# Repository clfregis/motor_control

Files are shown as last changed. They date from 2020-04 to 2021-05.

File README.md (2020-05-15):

# Motor Control Project
##### Prototype that controls a motor, get environment information and send it to an online database (firebase).

This project is a turnkey automation of a hopper in a industry. It consists of [hardware](hardware/) development of the board, development of the [firmware](firmware/) that manages the system, and a [web](web/) app that supervise and control the operation.
Basically, the board is able to control the motor, gather temperature and humidity information and send/receive data to/from a firebase database. How the system works is better explained in [firmware](firmware/) section.
______________
## 1. How to get things running

###  1.1. Hardware

First it is necessary to fabricate and mount the board:

1. Send GERBER files provided in [hardware](hardware/GERBER/) section to a PCB factory;
2. Buy components listed in [BOM](hardware/BOM.pdf) files;
3. Solder components in the board;

P.S.: It will be also necessary to buy a 5V power adapter (micro USB) to provide power to the board.

### 1.2. Web

Concurrently with hardware fabrication we can create a firebase project. We chose firebase because of its scalability and the built-in functions such as authentication and hosting.
There are some limitations in free plan, as shown [here](https://firebase.google.com/pricing?authuser=0). For MVP purposes, we will not be even closer to those limitations, but we can upgrade our plan if necessary.  
To create a project we need to have a google account, if you use Gmail, you already have one. Then access this [page](https://console.firebase.google.com/?pli=1), log in and create a `Realtime Database` (ust follows the steps in the tutorials, Google documentation is pretty awesome).
Then, add Firebase to your web app following these [instructions](https://firebase.google.com/docs/web/setup). **Attention!** In step 3, the HTMLs already have the SDKs. However, it is necessary to copy the snippet of our app's Firebase config object in the first line of `/web/js/main.js`.
After deploying the web app, we are ready!

### 1.3. Firmware

After mounting the hardware and deploying the web app, we are ready to build and flash the program in the ESP32. 

#### 1.3.1. Build
1. [Install the Espressif IoT Development Framework](https://github.com/espressif/esp-idf) or [link](https://docs.espressif.com/projects/esp-idf/en/latest/esp32/get-started/)
2. Make sure that the USB to UART driver of the development board is installed. In our case, the board uses [CP2102](https://www.silabs.com/products/development-tools/software/usb-to-uart-bridge-vcp-drivers)
3. Clone this repo: `git clone ...`
4. Inside the firmware folder, configure: `make menuconfig`
5. Build: `make all`
6. Flash: `make flash`

* Build & flash & monitor: `make flash monitor`

P.S.: If you get an error like: **"make" is not recognized as a internal or external command**. Try to use `idf.py` instead of `make` command.

Note: In step 3 you need to change some config values, for example:

* `Serial flasher config`. 
	+ `Default serial port`: Type the port at which the ESP32 is connected (e.g. COM3). If this option does not appear, just ignore it, the port will be automatically detected. 
	+ `Default baud rate`: Select 921600 for a faster flashing time.
* `Motor Configuration`. 
	+ `Motor Value`: Type the firebase child at which this ESP32 will send its data (e.g. motor_2).
	+ `Firebase address`: Type the firabase address without 'http://' (e.g. name_project.firebaseio.com). 
	+ (Optional) Change the `SP Time in seconds` value (It can be changed later via web app).
	+ `Timezone`: Select the time zone accordingly to your region.
	+ (Optional) `Log prints for Debug`, check it only if you want to see debug logs using the command prompt.
* `Example Connection Configuration`
	+ `Connect using`: Select WiFi.
	+ `WiFi SSID`: Type the SSID of your WiFi station.
	+ `WiFi Password`: Type the password of your WiFi station.

Save the changes and proceed to step 4.

### 1.4. Future Implementations

+ Update the daily and continuous operating times upon booting. Useful if the systems crashes during the day, because when it restarts it resets these values.
+ Every night at midnight, send the daily operating times to the server. Create a page on web app to display these values in bar graph format.
+ Implement a supervisor to reset the system if have problems with WiFi connection.

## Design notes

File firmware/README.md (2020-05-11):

# Firmware

______________

Well, depending on the project, the firmware development can be the most time consuming and complex task to do.
For this project, we used free RTOS mostly because it was necessary to deliver a robust application. Dealing with real motors, safety is a big concern.
For the microcontroller, we used ESP32, a very very powerful device (Arduinos are ancient technology compared to it). I will not get into too much detail regarding the specifications of the device. In general it has WiFi and Bluetooth connections, it is dual core, have some flash memory (used to store the SSID and Password of WiFi Networks) and can be easily programmed to work in Low Power.
Our application consists of a motor control of a hopper, based on the state of a NC switch. Basically, when the switch is not pressed (digital Low) the motor is running and when the switch is pressed (digital High) the motor stops. The system is also capable of retrieve the temperature and humidity of the environment using a DHT22 sensor. On top of that, we count the operation time of the motor. The operation time, temperature and humidity are stored internally and every minute it is sent to a database (we used firebase from Google).
We use the information of operation time for two things:

1. Stop the motor if it stays running for a long period of time (named SP time). Basically, when the motor runs for a long period of time, it means that the line breaks and material is being spilled outside the hopper.
2. Record the daily operation of the motor to cross check the material used daily.

## Global Variables

The global variables as in an ordinary code can be manipulated by all functions and all tasks. It is not good practice to use global variables in free RTOS, unless you really know what you are doing. The risk of a task change the value of a variable in the middle of execution of other task that also manipulates this same variable is high. We can use semaphores, queues and other things to maintain our code safe, however, in our case, there is only one task that ever writes to the variable (although many can read from it), then a global variable should not cause a problem.  
The variables, its type and its purpose are organized in the table below:

| Variable name | Type | For what it is used |
|---|---|---|
| temperature | uint8_t | Store the reading of the temperature |
| humidity | uint8_t | Store the reading of the humidity | 
| motorStatus | uint8_t | Store the status of the motor. 1-Running, 2-Halted, 0-Stopped |
| runningTime | time_t | Store the operation time of the motor since midnight |
| continuousRunningTime | time_t | Store the continuous operating time of the motor since the last time it was off |
| now | time_t | Store the current time of the system every time it is called by time() function |
| timeInfo | struct tm | Actually it is a struct not a variable, it stores the time in a very detailed way by localtime() function, taking into consideration timezone |
| url[65] | char | Store the firebase url to do the HTTP requests |
| bufferData[60][120] | char | Store the Data that will be sent to the database, up to 60 different POST request |
| bufferCounter | uint8_t | Counter used to do a loop when sending data to database |
| strftime_db[26] | char | For debug only, store a string with time in a human readable format |
| *motorAddress | static const char | Stores the value of the motor to create the url on connection with thedatabase. It is defined when programming the board on `menuconfig`, thus we pass`CONFIG_motorValue` to it |
| *firebaseAddress | static const char | Stores the address of the firebase to create the url on connection with thedatabase. It is defined when programming on `menuconfig`, thus we pass`CONFIG_firebaseAddress` to it |
| spTimesec | uint32_t | Stores the SP time of the motor. It can be changed by front end or when programming, thus we pass `CONFIG_SPTimesec` to it when programmin the board. |
| frontEndReset | uint8_t | Used to reset the motor by front end |
| updateBufferCounter | uint8_t | Used to count a defined number of seconds until the next update of the buffer |
| updateDailyFlag | bool | Used to check if the daily updating was already executed |
| gpio_evt_queue | xQueueHandle | Used to create a queue to handle GPIO events |

## Tasks

In free RTOS, we have tasks, which we can think of as pieces of codes that can run concurrently. The definition of a task is much more complex and I recommend to read the Kolban's book on ESP32 where he explains in details the architecture of a task. One thing to keep in mind is that tasks have priorities (the higher the number, higher is its priority), thus, let's say we have two tasks: A (priority 2) and B (priority 3). If A is running and B is ready to run, the task A will stop and then the task B will run. When B finishes, the task A will resume from where it stopped.
All tasks are shown in the table below.

| Task name | Priority |Function | Writes to  | Reads from |
|---|---|---|---|---|
| motor_control_task | 4 | Controls the motor operation, based on the state of NC switch, motor status and reset button|motorStatus, continuousRunningTime and frontEndReset|motorStatus|
| clock_task | 3 | Correct the drift time daily around midnight and reset the operation times|runningTime, continuousRunningTime,now and timeInfo| |
| motor_supervisor_task | 2 | Every other second reads temperature and humidity, updates the operation times and update the buffer|runningTime, continuousRunningTime, motorStatus, frontEndReset, bufferData size and bufferCounter |motorStatus and frontEndReset |
| database_task | 1 | Every other minute sends the buffer data to database, read SP time modifications in front end, update front end status and update daily status|url|size, bufferData, spTime and frontEndReset|

## Functions

|Function Name|Discussion|Parameters|Result|
|---|---|---|---|
|bufferUpdate|Take the values of tempertature, humidity, now, runningTime, motorStatus and continuousRunningTime and fetch to buffer|void|bufferData with a new value|
|update_sntp_time|Connect to SNTP server and update system time|void|System time synchronized with UTC time|
|get_last_value|It takes the last operation times for the current day|void|continuousRunningTime and runningTime updated|
|update_frontEndStatus|Connect to a child on firebase accordingly to the motorAddress and retrieve its status|motorStatusAddress pointer to motorAddress|frontEndStatus with a new value|
|get_sp_time|Connect to a child on firebase accordingly to the motorAddress and retrieve the SP time if it changed since last reading|motorSPAddress pointer to motorAddress|spTimesec with a new value|
|time_sync_notification_cb|For Debug purposes. Log on screen when the time is synchronized|*tv struct ??|Log on screen|
|obtain_time|Update now and timeInfo variables with current system time|local_now and local_timeinfo pointers to now and timeInfo variables|now and timeInfo with updated values|
|wifi_connection_start|Configures the WiFi variables|void|Returns error if configuration fails|
|wifi_connection_begin|Connect to WiFi in previous configured SSID|void|Returns error if connection fails|
|wifi_connection_end|Close the connection from WiFi network|void|Returns error if it fails|
|gpio_isr_handler|Runs every time an interrupt occurs, sending events to a queue|arg contains the number of gpio at wich the hardware interrupt happened|Send events to gpio event queue|
|http_event_handler|Handles HTTP event queue|evt pointer to HTTP event|Log accordingly to the content of event ID|
| update_daily | Sends data to database | motorDailyAddress Pointer to motorAddress| Database with updated daily operation information| 

## Future implementations

+ Separate files (one for function declarations and function definitions), one for tasks, etc.
+ Change temperature and humidity from uint_8 to float variables to have more precision.
+ Use some sort of automatic documentation generation from comments.

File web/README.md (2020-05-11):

# Web
______________

The `web` folder is basically the front end. It consists of the web interface, which request and send data to the firebase server.

## HTML

 The structure of HTML files is:
 
 	|-index.html
 	|---motor_1.html
 	|---motor_2.html
 	|---motor_3.html
 	|---motor_4.html
 	|-404.html (Generated by firebase)

 + `index.html` contains the intro page of the web app, which is a lateral bar and two cards. The first card contains links to open the motors pages. The second card will contain the input form to register new motors.
 + `404.html` contains the error page
 + `motor_X.html` are pages that show the graphs of each motor (temperature, humidity and operating) with respect to time. It is possible to zoom in the graphs using the mouse cursor or by choosing an especific date on the datepicker form. There are also cards that contain (almost) realtime information of the motor, such as its current state, temperature, daily operating times, etc. In this cards, it is possible to reset halted motors and change the SP time.

## CSS

 The structure of CSS files is:
 
 	|-all.css
 	|-dashboard.css
 	|-jquery-ui.css
 	|-reset.css

These files have all the styling definitions of every classes and objects inside the HTML files. The jquery-ui.css is special, it contains information specifically of the datepicker.

## JS

There are only one JS file, the `main.js`, which contains the interface to the firebase database and other stuff such as loading animations, functions to draw [zing charts](https://www.zingchart.com/download) and do [automatic zoom](https://www.zingchart.com/gallery/line-chart-with-zoom-buttons), functions to work with UNIX timestamp, etc. Please refer to [firebase documentation](https://firebase.google.com/docs/reference/js?authuser=0) to understand some of the functions used there. To use zing charts, please also check its [documentation](https://www.zingchart.com/docs/api/json-configuration)

## Firebase

For Firebase hosting, please refer to its [documentation](https://firebase.google.com/docs/hosting/?authuser=0#implementation_path). With respect to the database, we have pretty much the following structure:

	root {
		motor_1: {
			- M61_vCVgkNTwwjbF5MB : {
				CO: 60,
				D: 1588107627,
				DO: 60,
				H: 88,
				S: 1,
				T: 31
			},
			...
		},
		motor_2: {...},
		motor_3: {...},
		motor_4: {...},
		sp_time: {
			motor_1 : 200,
			motor_2 : 750,
			motor_3 : 800,
			motor_4 : 300
		},
		front_end_reset_status: {
			motor_1 : 200,
			motor_2 : 750,
			motor_3 : 800,
			motor_4 : 300
		},
		daily: {
			motor_1 : {
			- M61_vCVgkNTwwjbF5MB : {
				D: 1588107627,
				DO: 60
			},
		}

The `motor_X` childs receive informations from motors every minute. Back End writes to this child and Front End only reads. the format is the following:

	- M61_vCVgkNTwwjbF5MB : {
				CO: 60,
				D: 1588107627,
				DO: 60,
				H: 88,
				S: 1,
				T: 31
			},

 `- M61_vCVgkNTwwjbF5MB` is a timestamp key automatically created by firebase. It occurs because we are doing POST requests with this information. Each minute, up to 60 of this blocks are updated to the database by the motors, where:
	 
| Code 	| Meaning 	| Unit 	|
|---	|---	|---	|
| CO 	| Continuous Operation 	| Seconds 	|
| D 	| Date 	| UNIX timestamp format UTC timezone 	|
| DO 	| Daily Operation 	| Seconds 	|
| H 	| Humidity 	| % 	|
| S 	| Status 	| 0 - Off, 1 - Running, 2 - Halted 	|
| T 	| Temperature 	| ºC 	|

The `sp_time` child have the information of SP time operation of each motor. Front End writes to this child and Back End only reads (every minute).

The `front_end_reset_status` child is used by the Front End to reset the motor via the front end in case it is halted.

The `daily` child is used to store the information of the daily operation time of a day. Front end use this data to create a bar graph that is updated daily between 23:30 and 23:59 by the back end.

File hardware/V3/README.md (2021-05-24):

# Hardware V3
______________

## 3D Model of the board when mounted

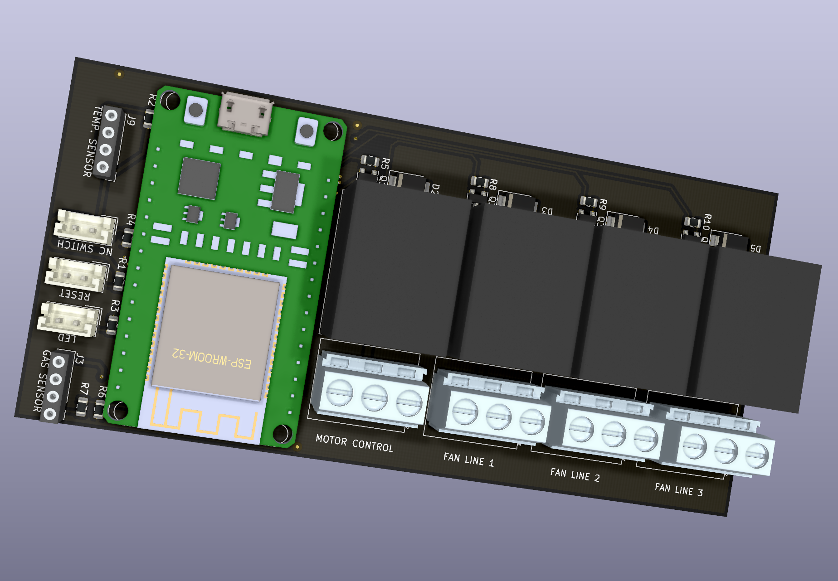
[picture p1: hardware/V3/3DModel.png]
3D Model


______________

The `hardware` folder has all necessary files to produce and mount the hardware part of the project as can be seen on the table below.

|File/Folder |Function |
|---|---|
|3DModel.png |3D Model picture of the mounted board. |
|ibom.html |Bill of Materials, all components necessary to build the project. |
|ESP32-pinout-mapping.png |Pinout of the development board used in the project. |
|gerber.zip |Output files to produce the PCB in the factory. The industries accept .zip files.|
|Schematic.pdf |File that shows how the components are connected to each other in the board. |
|Layout.pdf |Mechanical design |

We have two options when mounting this board, one is to solder the ESP32 Development Board directly to PCB, other is use female headers. The latter is better because it will be possible to remove the board easily if you want to.
It is important to be aware of what model of ESP 32 Development board to use. This project was designed to be compatible with [DoIT ESP32 DevKit V1](https://docs.platformio.org/en/latest/boards/espressif32/esp32doit-devkit-v1.html) with 30 pins (some development boards have more pins). The pinout is shown below:
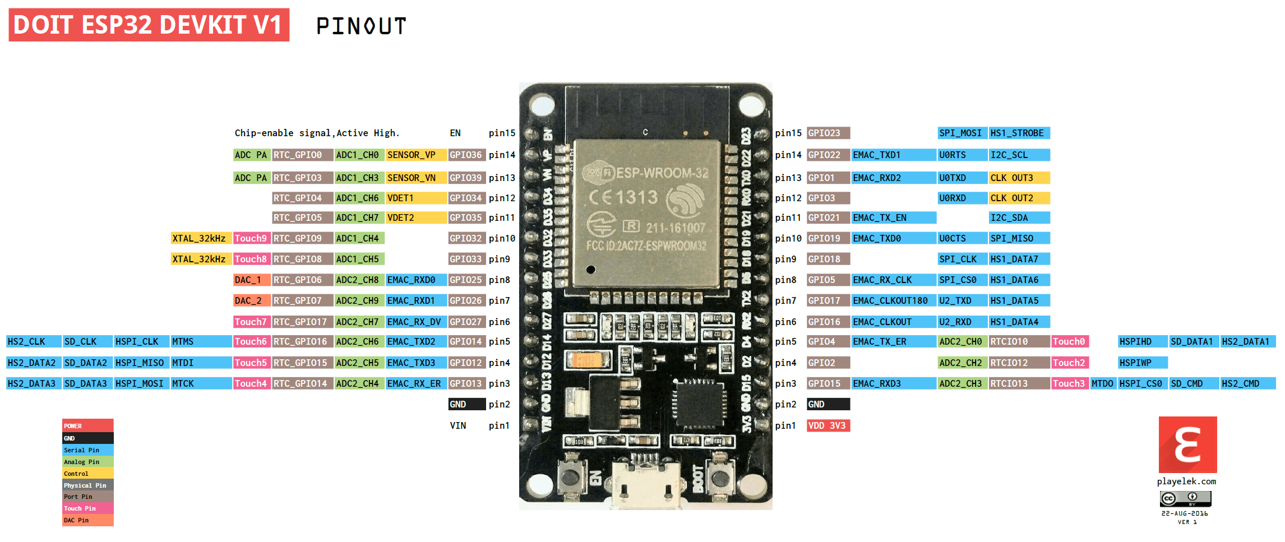
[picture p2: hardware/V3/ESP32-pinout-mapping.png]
DoIT ESP32 DevKit V1


## BOM

[Interactive BOM link](ibom.html)
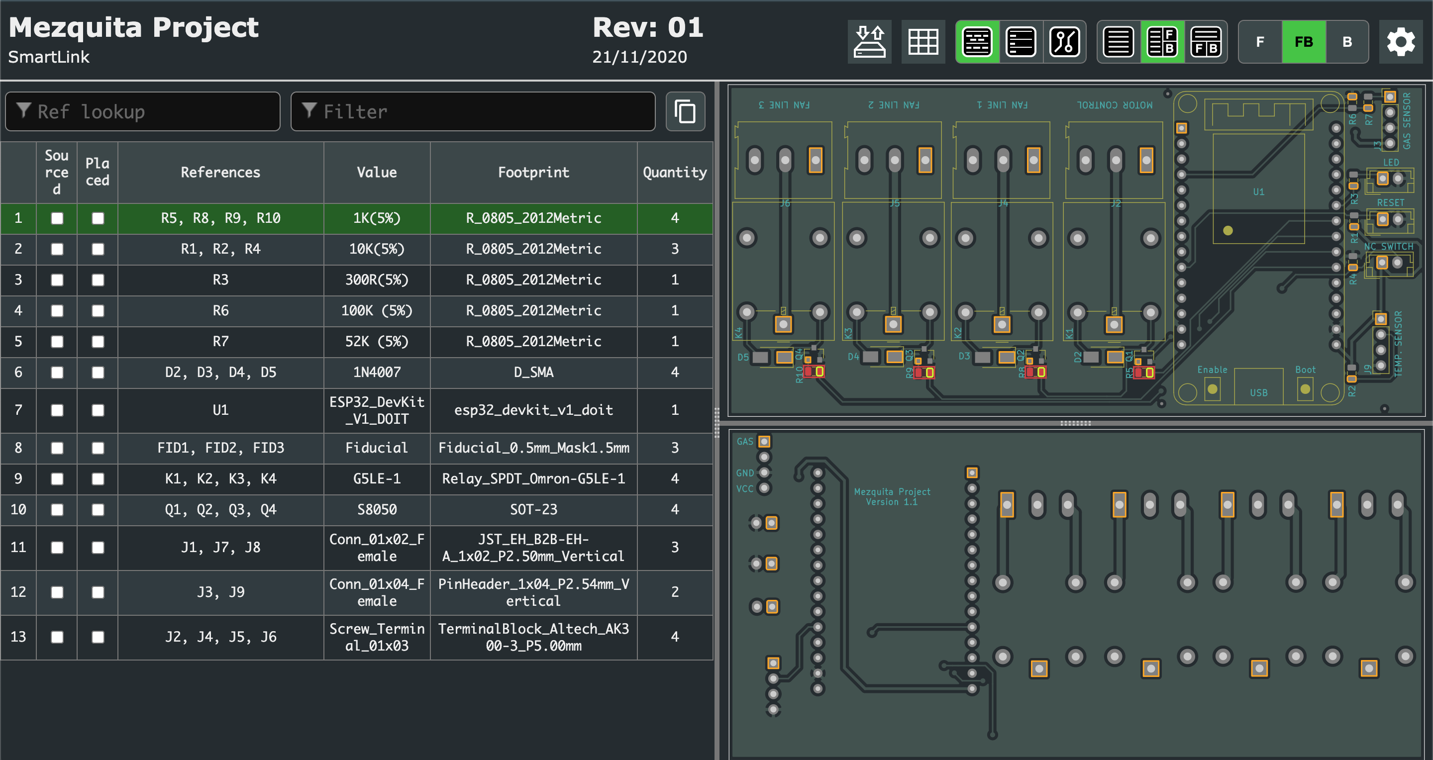
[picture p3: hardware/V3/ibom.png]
ibom


## Future Implementations

+ Add [licensing](https://forum.mysensors.org/topic/3096/open-hardware-licensing).
+ Add LEDs to show operation processes (blink fast when looking for internet connection, blink slow when is working properly, etc).
+ Instead of using DoIT ESP32 DevKit V1 board, put the ESP32 microcontroller directly into PCB.

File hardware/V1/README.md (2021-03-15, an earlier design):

# Hardware V1
______________

## 3D Model of the board when mounted

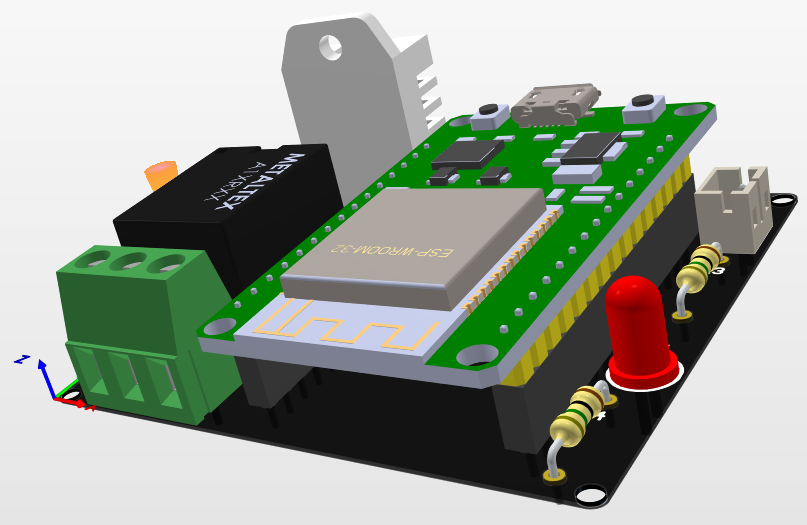
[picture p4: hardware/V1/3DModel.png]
3D Model


______________

The `hardware` folder has all necessary files to produce and mount the hardware part of the project as can be seen on the table below.

|File/Folder |Function |
|---|---|
|GERBER |Output files to produce the PCB in the factory. |
|3DModel.png |3D Model picture of the mounted board. |
|BOM.csv |Bill of Materials, all components necessary to build the project. |
|BOM.pdf |Bill of Materials, all components necessary to build the project. |
|Board 3D.pdf |3D Model picture of the mounted board. Open in Acrobat Reader. |
|Drill.Cam |Mechanical positioning and sizes of holes in the board in CAM format. |
|ESP32-pinout-mapping.png |Pinout of the development board used in the project. |
|GERBER.zip |Output files to produce the PCB in the factory. The industries accept .zip files.|
|General_Schematic.pdf |File that shows how the components are connected to each other in the board. |
|Layers.Cam |Mechanical positioning and sizes of all layers in the board in CAM format. |
|Mechanical Bot Mirrored.pdf|Mechanical designes with sizes and holes distances. |
|Mechanical Bot.pdf |Mechanical designes with sizes and holes distances. |
|Mechanical Top.pdf |Mechanical designes with sizes and holes distances. |	

For this specific project we do not have any special part, no SMD nor difficult components to find and use. We have two options when mounting this board, one is to solder the ESP32 Development Board directly to PCB, other is use female headers. The latter is better because it will be possible to remove the board easily if you want to.
It is important to be aware of what model of ESP 32 Development board to use. This project was designed to be compatible with [DoIT ESP32 DevKit V1](https://docs.platformio.org/en/latest/boards/espressif32/esp32doit-devkit-v1.html) with 30 pins (some development boards have more pins). The pinout is shown below:
DoIT ESP32 DevKit V1

## BOM

|Designator|Comment |Description |Quantity|Value |Reference Link |Datasheet|
|---|---|---|---|---|---|---|
|D1 |Diode |Rectifier Diode 1N4007 |1 |1N4007|[1N4007](https://lcsc.com/product-detail/Others_GW-1N4007_C331633.html) |[1N4007](Datasheet/1N4007.pdf)|
|L1 |Red LED |5mm Red LED |1 | |[5mm Red LED](https://lcsc.com/product-detail/Others_TOGIALED-TJ-L5FYTGHRMBCSFLC4R-A5_C331027.html)|[5mm Red LED](Datasheet/RED%20LED.pdf)|
|Q1 |Transistor |NPN General Purpose Amplifier |1 |PN2222|[PN2222](https://lcsc.com/product-detail/Transistors-NPN-PNP_ON-Semiconductor-ON-PN2222ATFR_C184875.html)|[PN2222](Datasheet/PN2222.pdf)|
|R1 |Resistor |1/4 W Resistor 1K 5% |1 |1K |[1K](https://lcsc.com/product-detail/Carbon-Film-Resistors_CCO-Chian-Chia-Elec-CF1-4W-1KR-5-T52_C120055.html)|[1K](Datasheet/1K%201_4W%20Resistor.pdf)|
|R2, R3, R5|Resistor |1/4 W Resistor 10K 5% |3 |10K |[10K](https://lcsc.com/product-detail/Carbon-Film-Resistors_UNI-ROYAL-Uniroyal-Elec-CFR0W4J0103A50_C61299.html)|[10K](Datasheet/10K%201_4W%20Resistor.pdf)|
|R4 |Resistor |1/4 W Resistor 300R 5% |1 |300R  |[300R](https://lcsc.com/product-detail/Carbon-Film-Resistors_UNI-ROYAL-Uniroyal-Elec-CFR0W4J0301A50_C69881.html)|[300R](Datasheet/300R%201_4W%20Resistor.pdf)|
|RLY1 |Relay |5V Relay |1 | |[5V](https://lcsc.com/product-detail/Relays_SRD-05VDC-SL-C_C35449.html)|[5V](Datasheet/5V%20Relay.pdf)|
|S1 |Switch |Switch Pushbutton |1 | |[Switch](https://lcsc.com/product-detail/Tactile-Switches_Korean-Hroparts-Elec-K2-6639DP-V4SW-04_C89914.html)|[Switch](Datasheet/Switch%20Pushbutton.pdf)|
|T1 |Terminal |3-Way Screw Terminal |1 | |[Screw Terminal](https://lcsc.com/product-detail/Screw-terminal_DIBO-DB126V-5-0-3P_C395850.html)|[Screw Terminal](Datasheet/ScrewTerminal.pdf)|
|T2 |JST |JST Male Board Connector |1 | |[JST Connector](https://lcsc.com/product-detail/Wire-To-Board-Wire-To-Wire-Connector_JST-Sales-America_B2B-XH-2-LF-SN_JST-Sales-America-B2B-XH-2-LF-SN_C158014.html)|[JST Connector](Datasheet/JST%20Connector.pdf)|
|T3,T4 |Not in Schematic (Optional)|Female Pin Header 15x2.54mm (Pitch)|2 | |[Pin Header](https://lcsc.com/product-detail/Pin-Header-Female-Header_Ckmtw-Shenzhen-Cankemeng-C124408_C124408.html)|[Pin Header](Datasheet/Female%20Pin%20Header.pdf)|
|U1 |ESP32 Dev Kit V1 |DoIT Development board |1 | |[ESP32](https://produto.mercadolivre.com.br/MLB-1027131279-esp32-placa-de-desenvolvimento-wifi-bluetooth-esp32s-_JM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)|[ESP32](https://github.com/SmartArduino/SZDOITWiKi/wiki/ESP8266---ESP32)|
|U2 |DHT22 |Temperature and Humidity Sensor |1 | |[DHT22](https://produto.mercadolivre.com.br/MLB-1144947807-sensor-de-temperatura-e-umidade-dht22-_JM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)|[DHT22](Datasheet/DHT22.pdf)|

## Future Implementations

+ Add [licensing](https://forum.mysensors.org/topic/3096/open-hardware-licensing).
+ Change PTH to SMD components to reduce size.
+ Add LEDs to show operation processes (blink fast when looking for internet connection, blink slow when is working properly, etc).
+ Instead of using DoIT ESP32 DevKit V1 board, put the ESP32 microcontroller directly into PCB.

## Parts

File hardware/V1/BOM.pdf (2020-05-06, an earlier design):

Designator | Comment | Description | Quantity | Value | Reference Link
D1 | Diode | Rectifier Diode 1N4007 | 1 | 1N4007 | 1N4007
L1 | Red LED | 5mm Red LED | 1 | | 5mm Red LED
Q1 | Transistor | NPN General Purpose Amplifier | 1 | PN2222 | PN2222
R1 | Resistor | 1/4 W Resistor 1K 5% | 1 | 1K | 1K
R2, R3, R5 | Resistor | 1/4 W Resistor 10K 5% | 3 | 10K | 10K
R4 | Resistor | 1/4 W Resistor 300R 5% | 1 | 300R | 300R
RLY1 | Relay | 5V Relay | 1 | | 5V
S1 | Switch | Switch Pushbutton | 1 | | Switch
T1 | Terminal | 3-Way Screw Terminal | 1 | | Screw Terminal
T2 | JST for the external switch | JST Male Board Connector | 1 | | JST Connector
T3,T4 | Not in Schematic (Optional) | Female Pin Header 15x2.54mm (Pitch) | 2 | | Pin Header
U1 | ESP32 Dev Kit V1 | DoIT Development board | 1 | | ESP32
U2 | DHT22 | Temperature and Humidity Sensor | 1 | | DHT22

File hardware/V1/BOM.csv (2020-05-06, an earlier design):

Designator | Comment | Description | Quantity | Value
D1 | Diode | Rectifier Diode 1N4007 | 1 | 1N4007
L1 | Red LED | 5mm Red LED | 1
Q1 | Transistor | NPN General Purpose Amplifier | 1 | PN2222
R1 | Resistor | 1/4 W Resistor 1K 5% | 1 | 1K
R2, R3, R5 | Resistor | 1/4 W Resistor 10K 5% | 3 | 10K
R4 | Resistor | 1/4 W Resistor 300R 5% | 1 | 300R
RLY1 | Relay | 5V Relay | 1
S1 | Switch | Switch Pushbutton | 1
T1 | Terminal | 3-Way Screw Terminal | 1
T2 | JST | JST Male Board Connector | 1
T3,T4 | Not in Schematic (Optional) | Female Pin Header 15x2.54mm (Pitch) | 2
U1 | ESP32 Dev Kit V1 | DoIT Development board | 1
U2 | DHT22 | Temperature and Humidity Sensor | 1

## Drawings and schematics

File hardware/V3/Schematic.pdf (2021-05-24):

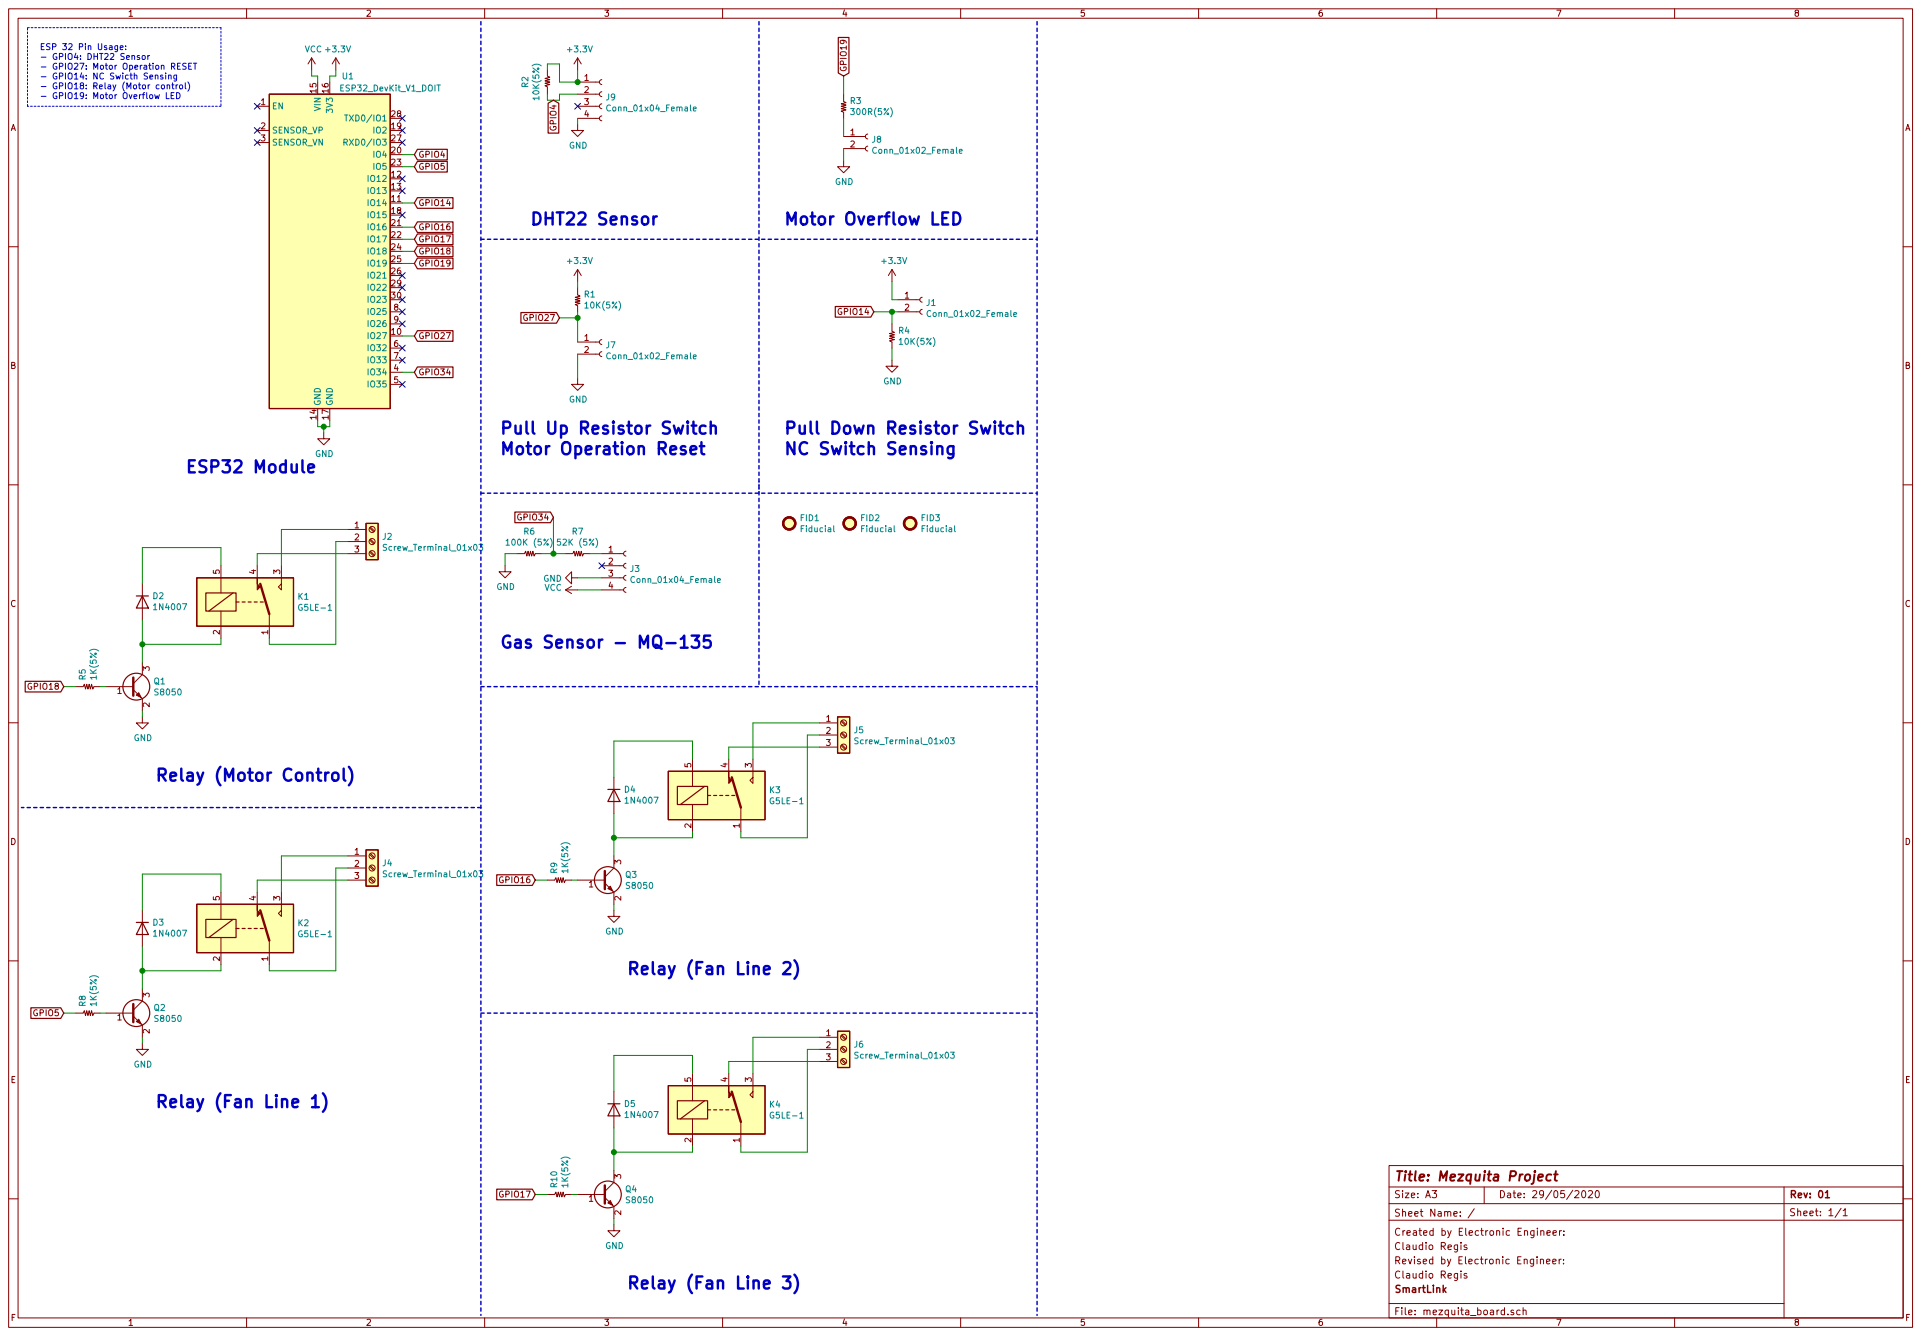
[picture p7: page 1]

ESP 32 Pin Usage: - GPIO4: DHT22 Sensor

Pull Up Resistor Switch
Motor Operation Reset

File: mezquita_board.sch Sheet Name: / SmartLink Claudio Regis

Claudio Regis
Revised by Electronic Engineer:

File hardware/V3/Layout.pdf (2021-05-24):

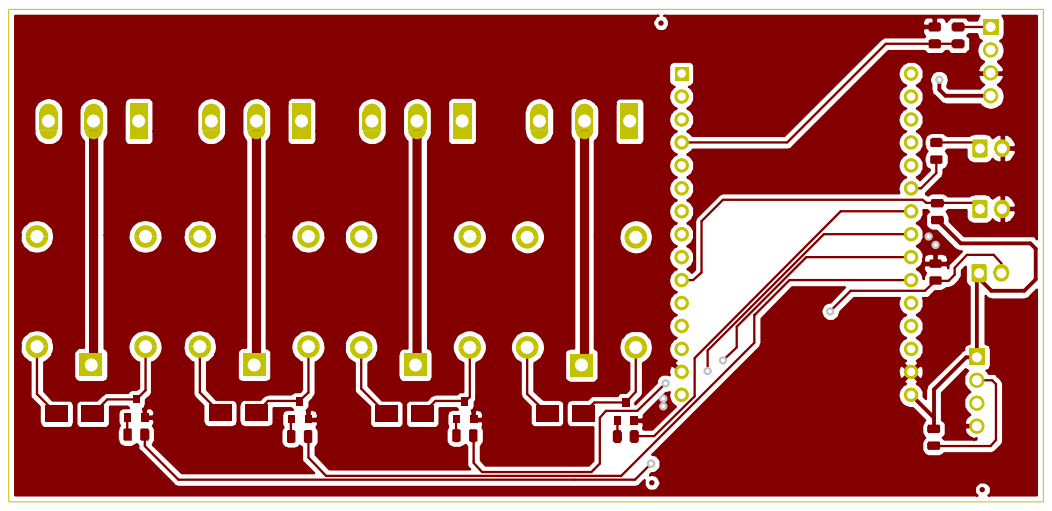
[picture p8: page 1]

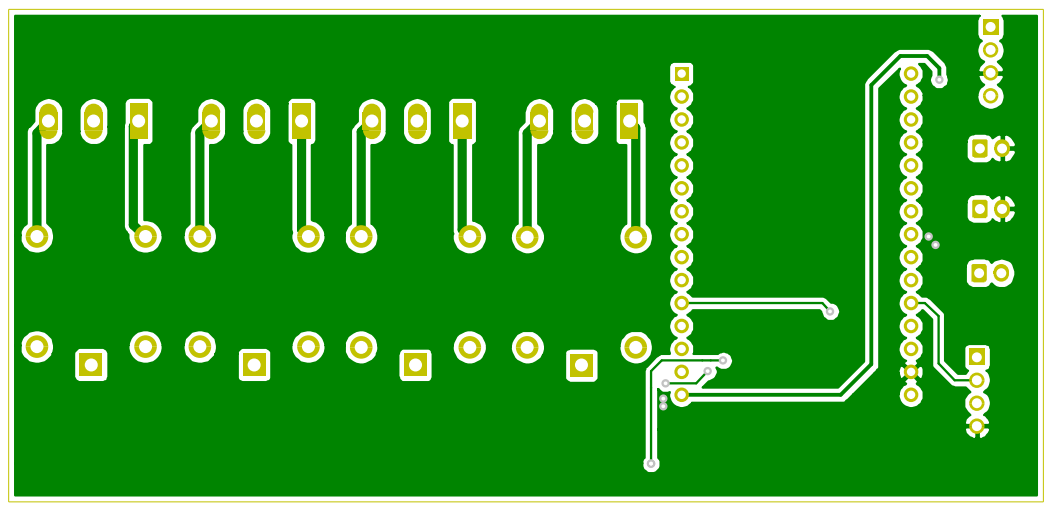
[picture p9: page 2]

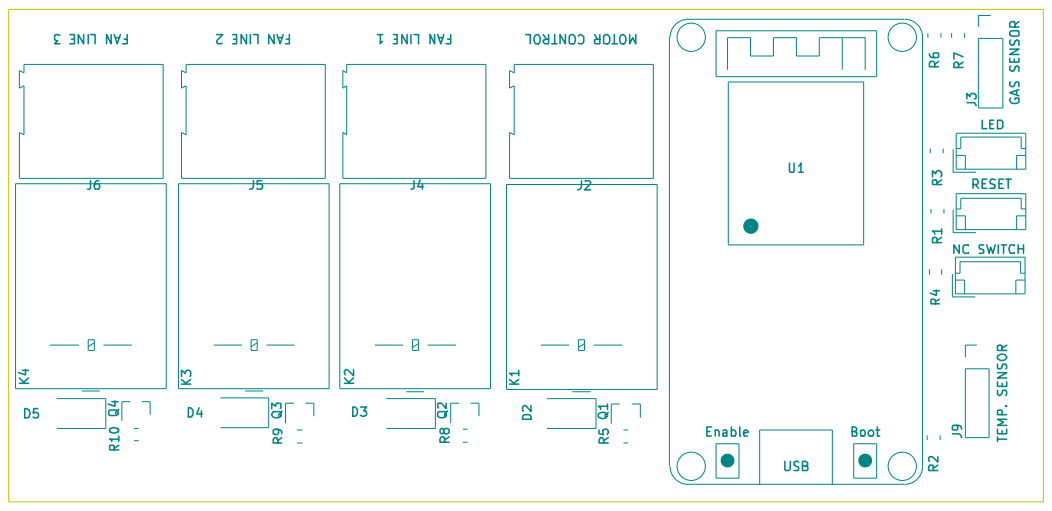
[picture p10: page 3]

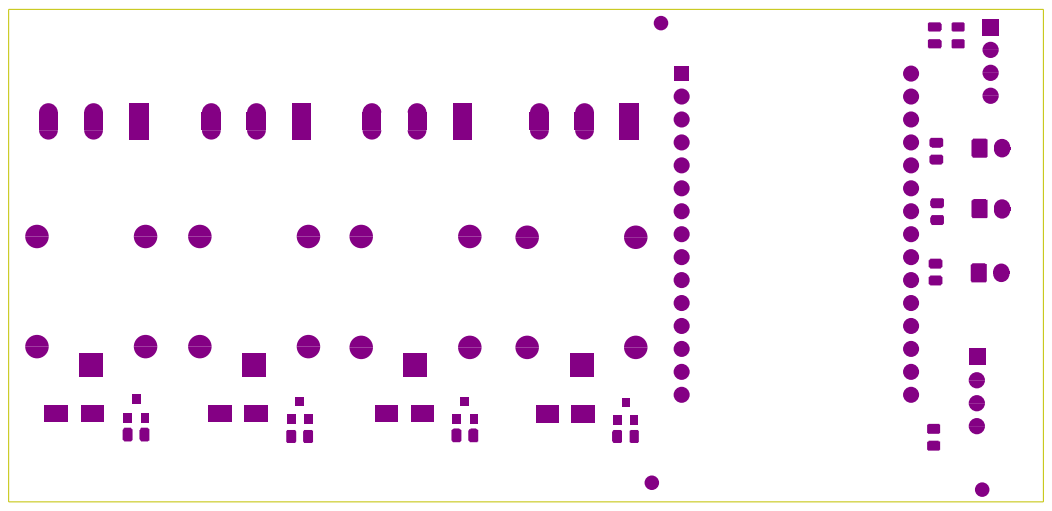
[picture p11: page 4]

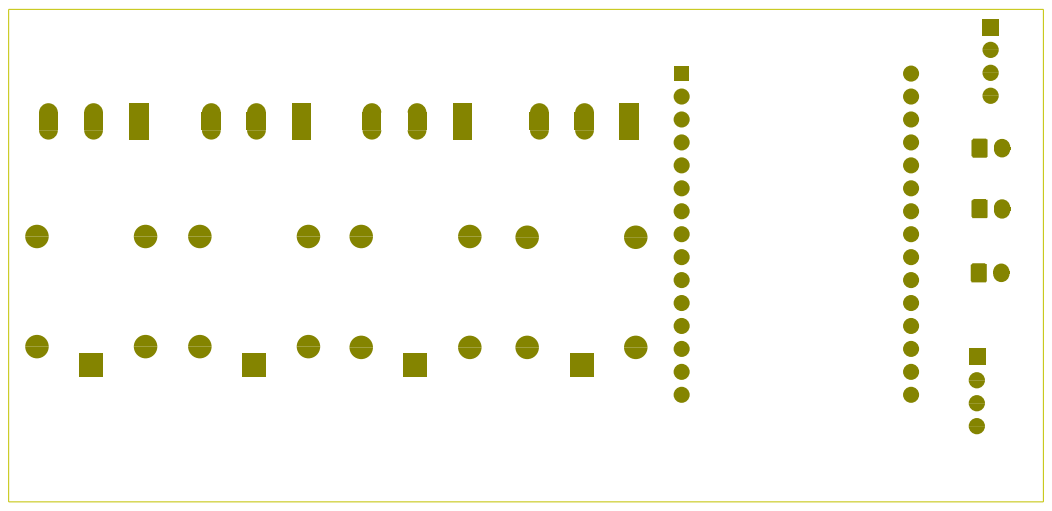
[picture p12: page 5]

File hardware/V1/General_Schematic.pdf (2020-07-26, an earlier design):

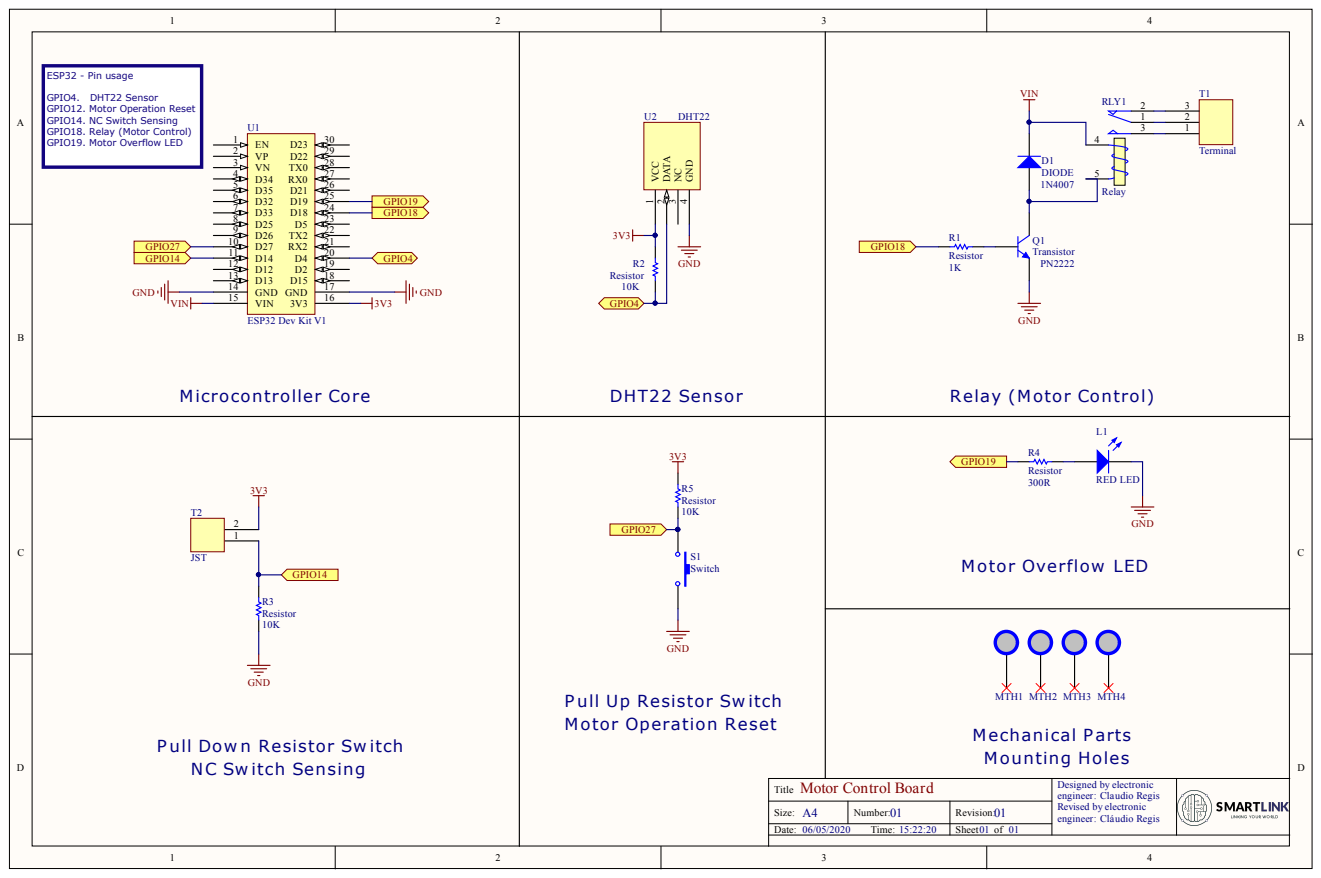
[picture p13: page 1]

P ull Up Resistor Sw itch
Motor Operation Reset

P ull Dow n Resistor Sw itch
NC Sw itch Sensing

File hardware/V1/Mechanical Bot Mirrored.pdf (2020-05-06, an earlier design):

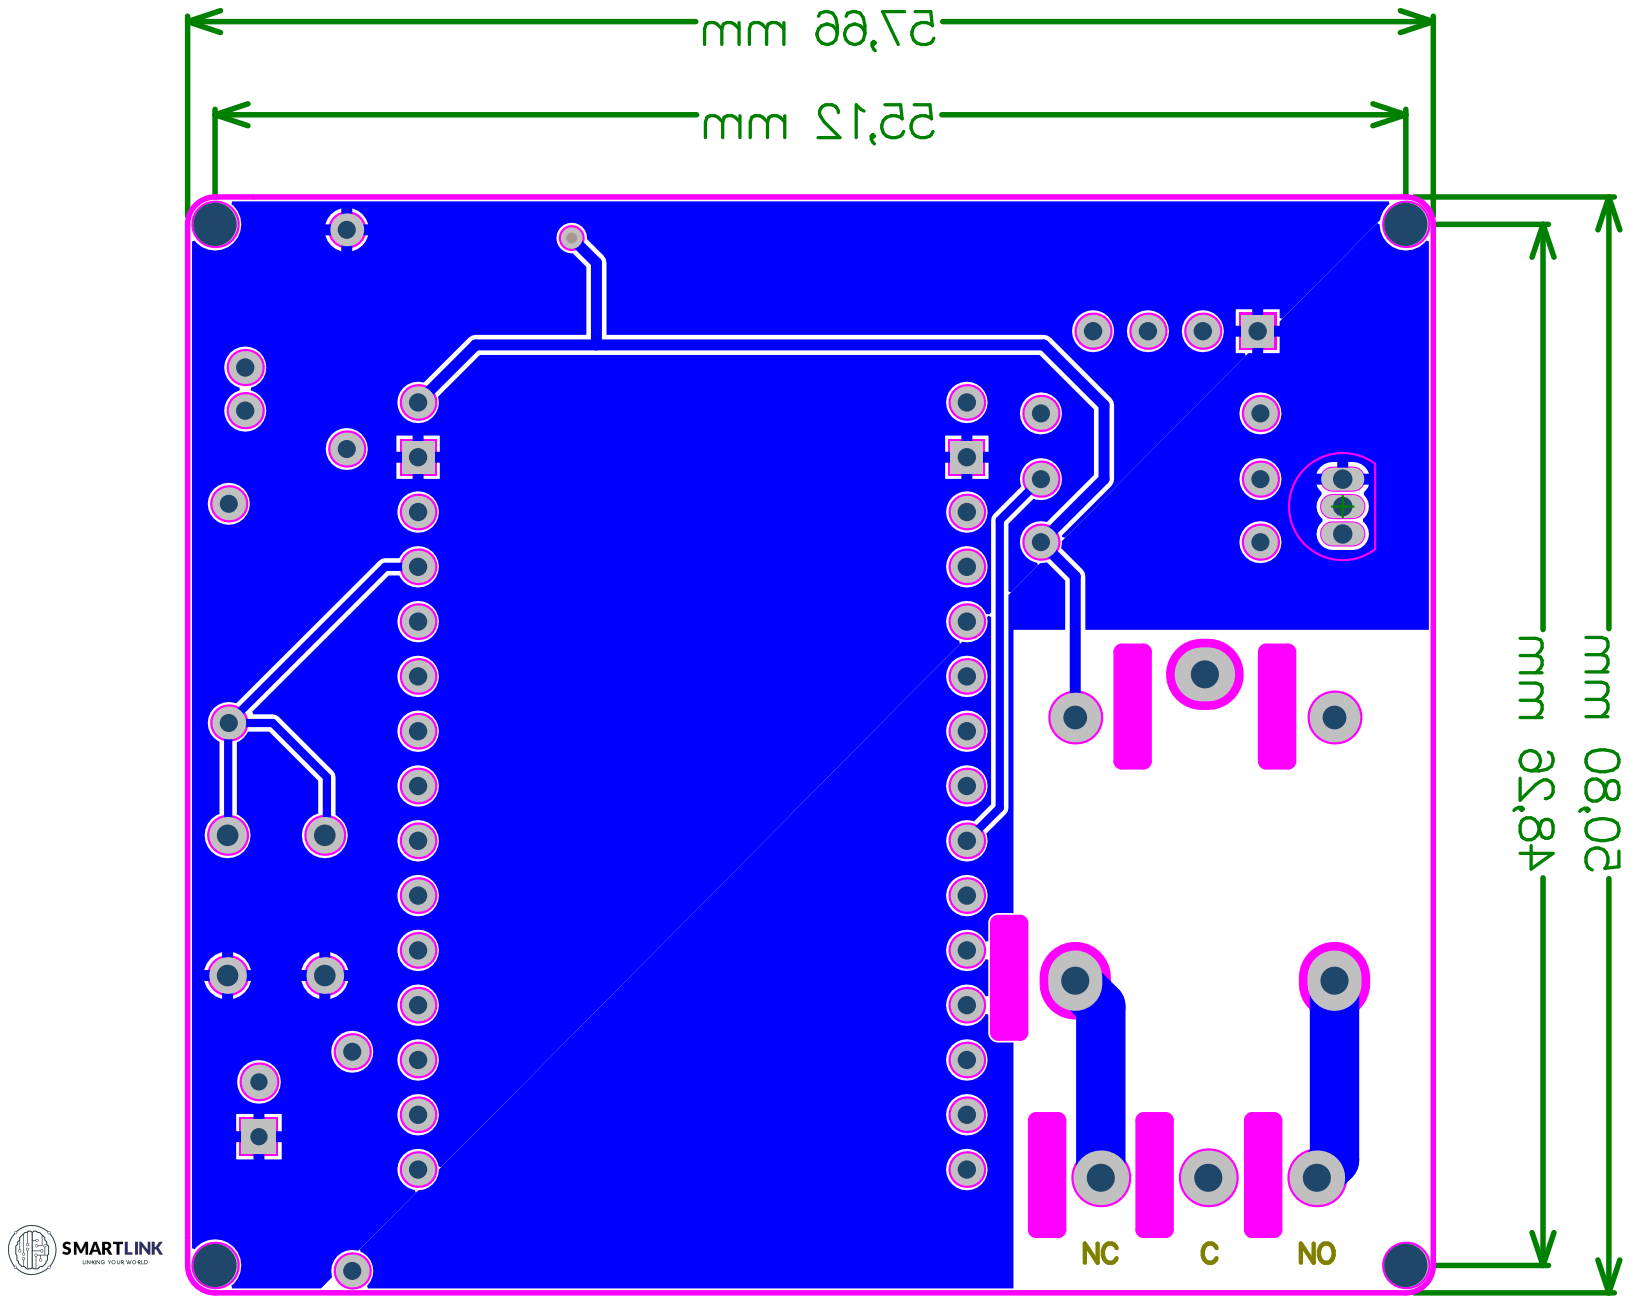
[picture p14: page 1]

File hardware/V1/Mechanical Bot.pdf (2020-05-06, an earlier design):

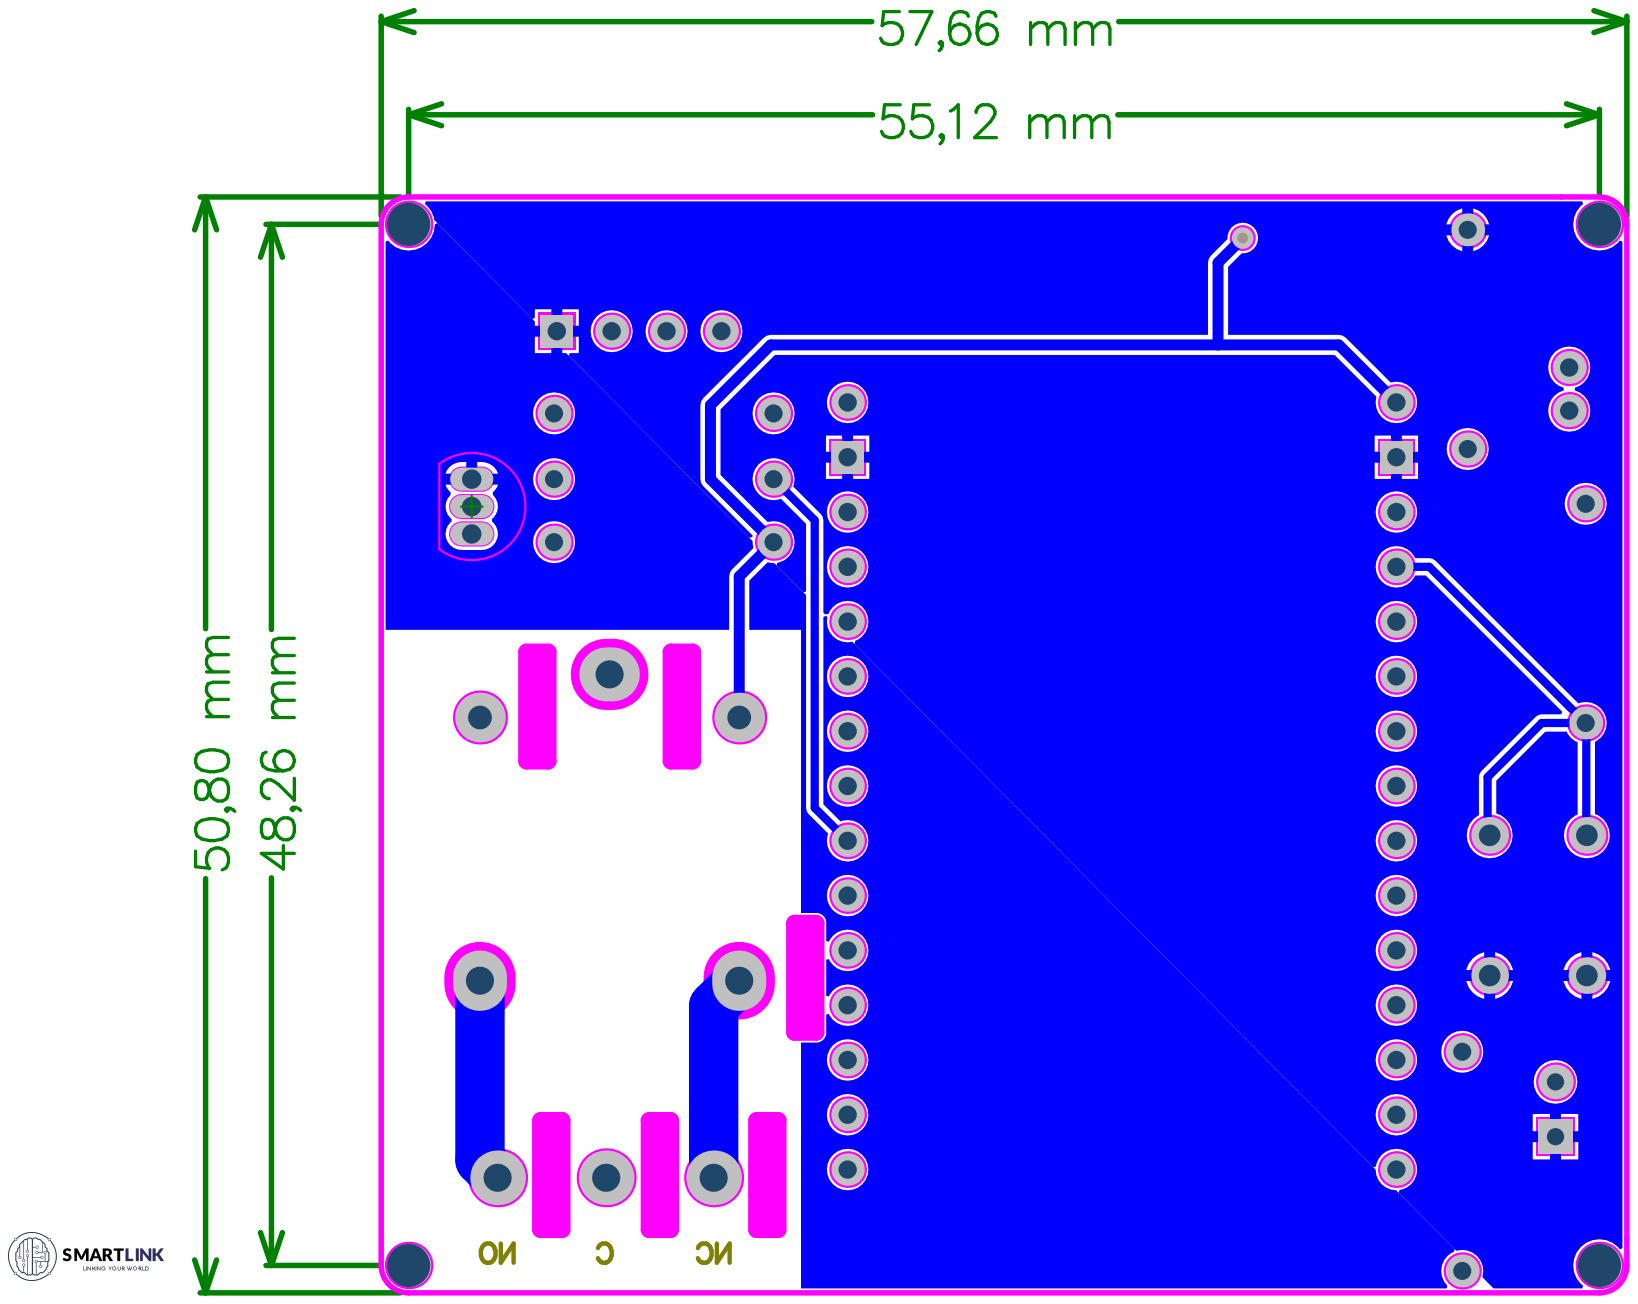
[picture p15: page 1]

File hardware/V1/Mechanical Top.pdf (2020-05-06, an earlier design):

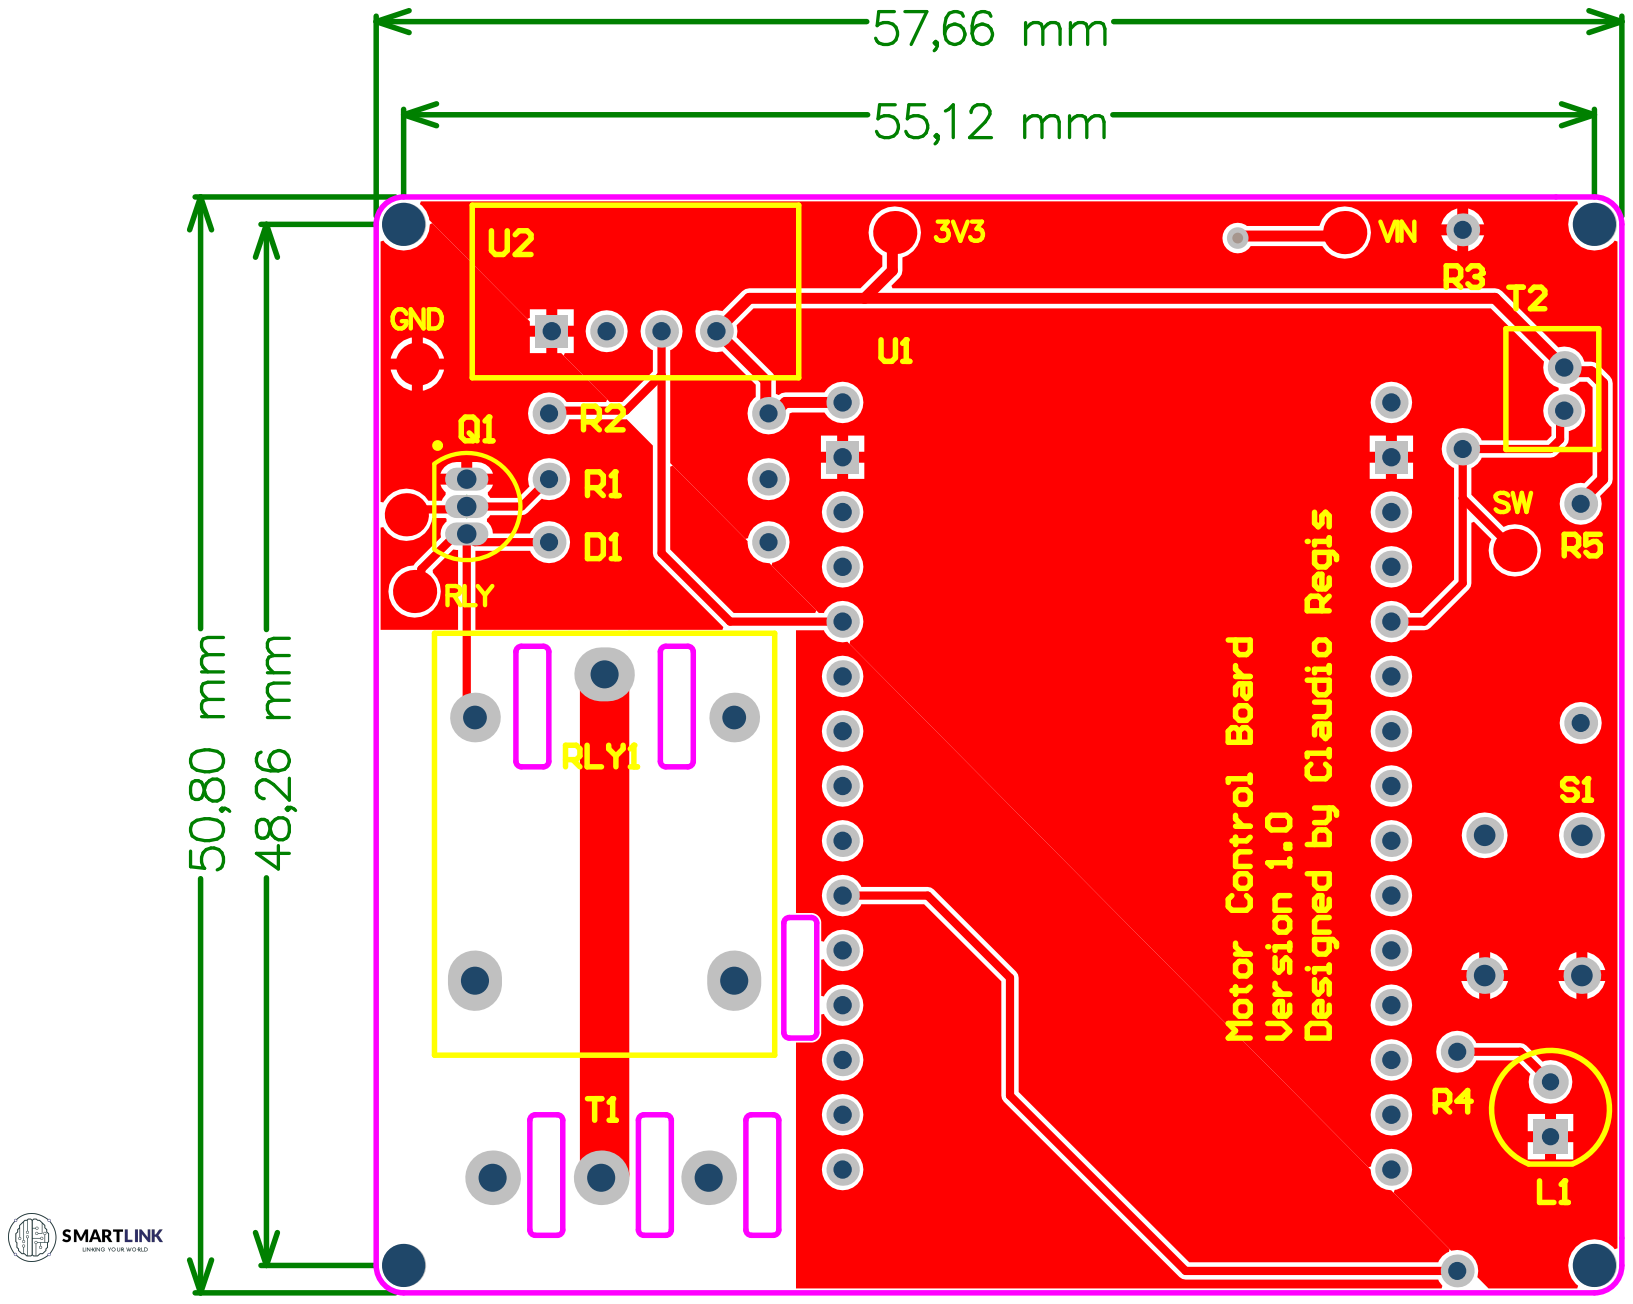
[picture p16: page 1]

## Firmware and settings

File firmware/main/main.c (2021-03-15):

/**
 * Motor Control:
 *
 * Code created by engineer Claudio Regis in 06 of April of 2020, Quarantine day 12.
 *
**/

#include <stdio.h>
#include <string.h>
#include <stdlib.h>
#include "freertos/FreeRTOS.h"
#include "freertos/task.h"
#include "freertos/queue.h"
#include "freertos/event_groups.h"
#include "driver/gpio.h"
#include "driver/adc.h"
#include "esp_adc_cal.h"
#include <dht11.h>
#include <time.h>
#include <sys/time.h>
#include "esp_system.h"
#include "esp_event.h"
#include "esp_log.h"
#include "esp_attr.h"
#include "esp_sleep.h"
#include "nvs_flash.h"
//#include <protocol_examples_common.h>
#include "esp_sntp.h"

#include "esp_wifi.h"
#include "esp_event_loop.h"
#include "tcpip_adapter.h"
#include "esp_tls.h"
#include "esp_http_client.h"
#include "lwip/err.h"
#include "lwip/sockets.h"
#include "lwip/sys.h"
#include "lwip/netdb.h"
#include "lwip/dns.h"
#include "cjson.h"

/**
 * Brief:
 *
 * GPIO status:
 * GPIO4:   data
 * GPIO12:  input DEPRECATED. It is not possible to use pin 12 during bootup since it is connected to flash chip
 * GPIO27:  input
 * GPIO14:  input, pulled up, interrupt from rising edge and falling edge
 * GPIO18:  output
 * GPIO19:  output
 *
 * Connection:
 * Connect GPIO4 with DHT sensor
 * Connect GPIO27 Reset Button
 * Connect GPIO14 with NC switch
 * Connect GPIO18 with relay (Motor)
 * Connect GPIO19 with LED Overflow
 *
 **/


#define GPIO_OUTPUT_IO_0        18  // Motor pin (will control a relay)
#define GPIO_OUTPUT_IO_1        19  // LED pin 
#define GPIO_OUTPUT_PIN_SEL     ((1ULL<<GPIO_OUTPUT_IO_0) | (1ULL<<GPIO_OUTPUT_IO_1))
#define GPIO_INPUT_IO_0         14  // NC Switch pin
#define GPIO_INPUT_IO_1         27  // Reset Button
#define GPIO_INPUT_PIN_SEL      ((1ULL<<GPIO_INPUT_IO_0) | (1ULL<<GPIO_INPUT_IO_1))
#define GPIO_DATA_0             4   // DHT11 Sensor on the final code, try to use a DHT22 library
#define ESP_INTR_FLAG_DEFAULT   0
#define DEFAULT_VREF    1100        //Use adc2_vref_to_gpio() to obtain a better estimate
#define NO_OF_SAMPLES   64          //Multisampling

//==========================
// Function definitions
//==========================
/*!
 * @function    bufferUpdate
 * @abstract    Update the buffer with current values
 * @discussion  This function take the values of tempertature, 
 *              humidity, now, runningTime, motorStatus and 
 *              continuousRunningTime and fetch to buffer
 * @result      bufferData with a new value
*/
static void bufferUpdate(void);
/*!
 * @function    update_sntp_time
 * @abstract    Connect to SNTP server and update system time
 * @discussion  This function connects to WiFi, then connects
 *              to a SNTP server, update the system time
 *              then disconnets from WiFi
 * @result      System time synchronized
*/
static void update_sntp_time(void);
/*!
 * @function    get_last_value
 * @abstract    Updates the last operation times for the current day
 * @discussion  This function connects to WiFi, then connects
 *              to a firebase server, take the last update operation
 *              times, compare its timestamp with current time. If
 *              the last value is from the current day, update runningTime
                and continuousRunningTime
 * @result      continuousRunningTime and runningTime updated
*/
static void get_last_value(void);
/*!
 * @function    update_frontEndStatus
 * @abstract    Retrieve the Front End Status
 * @discussion  This function connects to WiFi, then connects
 *              to a firebase server directly on the specific
 *              child that contains the front end status and
 *              store its value on frontEndReset
 * @param       motorStatusAddress      Pointer to motorAddress
 * @result      continuousRunningTime and runningTime updated
*/
static void update_frontEndStatus(char *motorStatusAddress);
/*!
 * @function    get_sp_time
 * @abstract    Retrieve the SP time
 * @discussion  This function connects to WiFi, then connects
 *              to a firebase server directly on the specific
 *              child that contains the SP time and
 *              store its value on spTimesec
 * @param       motorSPAddress      Pointer to motorAddress
 * @result      spTimesec with a new value
*/
static void get_sp_time(char *motorSPAddress);
/*!
 * @function    time_sync_notification_cb
 * @abstract    Notification of time synchronization
 * @discussion  For Debug purposes. Log on screen
 *              when the time is synchronized
 * @param       tv      Pointer to a timeval struct??
 * @result      Logs on screen
*/
void time_sync_notification_cb(struct timeval *tv);

/*!
 * @function    obtain_time
 * @abstract    Get system time 
 * @discussion  Update now and timeInfo variables with 
 *              current system time
 * @param       local_now           pointer to now
 * @param       local_timeinfo      pointers to timeInfo
 * @result      now and timeInfo with updated values
*/
static void obtain_time(time_t *local_now, struct tm *local_timeinfo); // only need this function to check if it is midnight
/*!
 * @function    wifi_connection_start
 * @abstract    Configures the WiFi variables
 * @discussion  This helper function configures Wi-Fi 
 *              or Ethernet, as selected in menuconfig.
 *              Read "Establishing Wi-Fi or Ethernet Connection" 
 *              section in examples/protocols/README.md for
 *              more information about this function.
 * @result      Returns error if configuration fails
*/
static void wifi_connection_start(void);
/*!
 * @function    wifi_connection_begin
 * @abstract    Connect to WiFi in previous configured SSID
 * @discussion  This helper function configures Wi-Fi 
 *              or Ethernet, as selected in menuconfig.
 *              Read "Establishing Wi-Fi or Ethernet Connection" 
 *              section in examples/protocols/README.md for
 *              more information about this function.
 * @result      Returns error if connection fails
*/
static void wifi_connection_begin(void);
/*!
 * @function    wifi_connection_end
 * @abstract    Close the connection from WiFi network
 * @discussion  This helper function configures Wi-Fi 
 *              or Ethernet, as selected in menuconfig.
 *              Read "Establishing Wi-Fi or Ethernet Connection" 
 *              section in examples/protocols/README.md for
 *              more information about this function. 
 * @result      Returns error if it fails
*/
static void wifi_connection_end(void);
/*!
 * @function    _http_event_handler
 * @abstract    Handles HTTP event queue    
 * @discussion  Logs and some stuff based on HTTP event
 * @param       evt           pointer to HTTP event 
 * @result      Log accordingly to the content of event ID
*/
esp_err_t _http_event_handler(esp_http_client_event_t *evt);
/*!
 * @function    gpio_isr_handler
 * @abstract    Handles hardware interrupts   
 * @discussion  Runs every time an interrupt occurs, 
 *              sending events to a queue
 * @param       arg           contains the number of gpio at wich the hardware interrupt happened
 * @result      Send events to gpio event queue
*/
static void IRAM_ATTR gpio_isr_handler(void* arg);
/*!
 * @function    update_daily
 * @abstract    Sends data to database  
 * @discussion  Runs at midnight to update the daily operation time
 * @param       motorDailyAddress      Pointer to motorAddress
 * @result      database with updated daily operation information
*/

static void update_daily(char *motorDailyAddress);
static esp_err_t event_handler(void *ctx, system_event_t *event);
int startsWith(const char *a, const char *b);
static void check_efuse(void);
static void print_char_val_type(esp_adc_cal_value_t val_type);
//==========================
// End Function definitions
//==========================


//==========================
// Variable definitions
//==========================
// Create a global variable of type uint8_t to store temperature and another to store humidity
uint8_t temperature = 0;
uint8_t humidity = 0;
uint32_t adc_reading = 0;
uint32_t voltage = 0;
// Global variables to handle the status of the motor
uint8_t motorStatus = 0; // It starts off
time_t runningTime = 0;
time_t continuousRunningTime = 0;

time_t now;
struct tm timeInfo;

char url[65];
char bufferData[60][120];	//  { "T" : 28, "H" : "78", "S" : "ON", "D" : 12314554, "DO" : 1588033061, "CO" : 358 }
							// T=Temperature, H = Humidity, S=Status, D=Date, DO=Daily Operation, CO=Continuous Operation
							// Example
							/*{
								"CO" : 414,
								"D" : 1588033061,
								"DO" : 414,
								"H" : 91,
								"S": 1,
								"T" : 26
							}*/
uint8_t bufferCounter=0;
char strftime_db[26];
char *motorAddress = CONFIG_motorValue;
char *firebaseAddress = CONFIG_firebaseAddress;
uint32_t spTimesec = CONFIG_SPTimesec;
uint8_t frontEndReset = 0;
uint8_t updateBufferCounter=0;
bool updateDailyFlag = false;
// Create a global variable of type xQueueHandle, which is the type we need to reference a FreeRTOS queue.
static xQueueHandle gpio_evt_queue = NULL;
static EventGroupHandle_t wifi_event_group;
const int CONNECTED_BIT = BIT0;

static esp_adc_cal_characteristics_t *adc_chars;
static const adc_channel_t channel = ADC_CHANNEL_6;     //GPIO34 if ADC1, GPIO14 if ADC2
static const adc_atten_t atten = ADC_ATTEN_DB_0;
static const adc_unit_t unit = ADC_UNIT_1;

#if CONFIG_debug
    static const char *TAG = "LwIP SNTP";
    static const char *TAG_1 = "HTTP Request";
    static const char *TAG_2 = "Hour/Date";
    static const char *TAG_3 = "Queue Creation";
    static const char *TAG_4 = "Update values";
    static const char *TAG_DEBUG = "DEBUG";
    // For CONFIG_debug, to show in terminal the update time
    char strftime_buf[64];
#endif

//==========================
// End Variable definitions
//==========================


//==========================
// Tasks
//==========================

// Task that controls the motor operation
// Regarding to the NC switch values, motor status and reset button
void motor_control_task(void* arg) {	
    uint8_t io_num;
    // First we check the state of the button.
    if(gpio_get_level(GPIO_INPUT_IO_0)){
    	// NC not pressed
        // Turn on the motor
    	gpio_set_level(GPIO_OUTPUT_IO_0, 1);
    	// Update status
        motorStatus = 1;
    }
    else {
		// NC pressed
	    // Turn off the motor
    	gpio_set_level(GPIO_OUTPUT_IO_0, 0);
    	// Update status
        motorStatus = 0;
    }
    while(1) {
        // When receives an event on the gpio queue
        if(xQueueReceive(gpio_evt_queue, &io_num, portMAX_DELAY)) {
            if(io_num==GPIO_INPUT_IO_0 && gpio_get_level(io_num)==1 && motorStatus!=2) {
            	// NC not pressed
                // Turn on the motor
                gpio_set_level(GPIO_OUTPUT_IO_0, 1);
                // Update status
                motorStatus = 1;
            }
            if (io_num==GPIO_INPUT_IO_0 && gpio_get_level(io_num)==0 && motorStatus!=2) {
            	// NC pressed
                // Turn off the motor
                gpio_set_level(GPIO_OUTPUT_IO_0, 0);
                // Update status
                motorStatus = 0;
            }
            if(io_num==GPIO_INPUT_IO_1 && gpio_get_level(io_num)==0 && motorStatus==2) {
                // Reset Motor to its normal operation
                if(gpio_get_level(GPIO_INPUT_IO_0)==1){
                    // NC not pressed
                    // Turn on the motor
                    gpio_set_level(GPIO_OUTPUT_IO_0, 1);
                    // Update status
                    motorStatus = 1;
                }
                else if(gpio_get_level(GPIO_INPUT_IO_0)==0){
                    // NC pressed
                    // Turn off the motor
                    gpio_set_level(GPIO_OUTPUT_IO_0, 0);
                    // Update status
                    motorStatus = 0;
                }
                // Turn off Alert LED
                gpio_set_level(GPIO_OUTPUT_IO_1, 0);
                // Reset continuous time operation
                continuousRunningTime=0;
                frontEndReset=2;
            }
        }
    }
}

// Task that maintain and configure the time and date 
void clock_task(void *arg) {
    bool flagClock=false;

	while(1){
        // Every ten minutes, check if is midnight
        vTaskDelay(600000/portTICK_RATE_MS);

        obtain_time(&now, &timeInfo);

        // Correct the drift every night
        if (timeInfo.tm_hour==23 && timeInfo.tm_min>=30 && timeInfo.tm_min<=59){
            if (!flagClock){
                flagClock=true;
                updateDailyFlag = true;
                #if CONFIG_debug
                    ESP_LOGI(TAG, "Correct the drift, daily");
                #endif
                update_sntp_time();
                time(&now);
               
            }
        }
        else {
            flagClock=false;
        }
	}
}
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
void app_main() {
    //=============================
    // GPIO configuration
    //=============================

    gpio_config_t io_conf;

    // Disable interrupt
    io_conf.intr_type = GPIO_PIN_INTR_DISABLE;
    // Set as output mode
    io_conf.mode = GPIO_MODE_OUTPUT;
    // Bit mask of the pins that you want to set,e.g.GPIO18/19
    io_conf.pin_bit_mask = GPIO_OUTPUT_PIN_SEL;
    // Disable pull-down mode
    io_conf.pull_down_en = 0;
    // Disable pull-up mode
    io_conf.pull_up_en = 0;
    // Configure GPIO with the given settings
    gpio_config(&io_conf);
    // Start the gpio in Low value
    gpio_set_level(GPIO_OUTPUT_IO_0, 0);

    // Interrupt in any edge
    io_conf.intr_type = GPIO_INTR_ANYEDGE;
    // Bit mask of the pins, use GPIO4 here
    io_conf.pin_bit_mask = GPIO_INPUT_PIN_SEL;
    // Set as input mode    
    io_conf.mode = GPIO_MODE_INPUT;
    // Disable pull-down mode, using external pullup
    io_conf.pull_down_en = 0;
    // Disable pull-up mode, using external pullup
    io_conf.pull_up_en = 0;
    gpio_config(&io_conf);

    //=============================
    // End of GPIO configuration
    //=============================

    wifi_connection_begin();
    wifi_connection_start();

    //Check if Two Point or Vref are burned into eFuse
    check_efuse();

    //Configure ADC
    adc1_config_width(ADC_WIDTH_BIT_12);
    adc1_config_channel_atten(channel, atten);

    //Characterize ADC
    adc_chars = calloc(1, sizeof(esp_adc_cal_characteristics_t));
    esp_adc_cal_value_t val_type = esp_adc_cal_characterize(unit, atten, ADC_WIDTH_BIT_12, DEFAULT_VREF, adc_chars);
    print_char_val_type(val_type);

    //=============================
    // RTC configuration
    //=============================

    // https://github.com/nayarsystems/posix_tz_db/blob/master/zones.csv
    #ifdef CONFIG_Brazil 
        char *timeZone = "<-03>3";
    #else
        char *timeZone = "CST6CDT,M4.1.0,M10.5.0";
    #endif

    // Set timezone to Region
    setenv("TZ", timeZone, 1);
    // Apply
    tzset();

    obtain_time(&now, &timeInfo);

    // Is time set? If not, tm_year will be (1970 - 1900).
    if (timeInfo.tm_year < (2020 - 1900)) {
    	#if CONFIG_debug
    	    ESP_LOGI(TAG, "Time is not set yet. Connecting to WiFi and getting time over NTP.");
    	#endif
        update_sntp_time();
        time(&now);
        // obtain_time(&now, &timeInfo);
    }

    //=============================
    // End of RTC configuration
    //=============================

    get_last_value();



    /*  So, we will create a queue that can hold a maximum of 10 elements and since it will 
    *   contain integers, we can get the size of an integer in bytes with a call to the 
    *   sizeof function.
    */
    // Create a queue to handle gpio event from ISR
    gpio_evt_queue = xQueueCreate(10, sizeof(uint32_t));

    if(gpio_evt_queue == NULL) {
    	#if CONFIG_debug
    		ESP_LOGE(TAG_3, "Error creating the queue");
    	#endif
    }

    // Install gpio isr service
    gpio_install_isr_service(ESP_INTR_FLAG_DEFAULT);
    // Hook isr handler for specific gpio pin
    gpio_isr_handler_add(GPIO_INPUT_IO_0, gpio_isr_handler, (void*) GPIO_INPUT_IO_0);
    gpio_isr_handler_add(GPIO_INPUT_IO_1, gpio_isr_handler, (void*) GPIO_INPUT_IO_1);

    //=============================
    // Tasks initializations
    //=============================

    // Start motor supervisor task
    xTaskCreate(motor_control_task, "motor_control_task", 2048, NULL, 4, NULL);
    // Start motor supervisor task
    xTaskCreate(&motor_supervisor_task, "motor_supervisor_task", 2048, NULL, 3, NULL);
    // Start the database task
    xTaskCreate(&database_task, "database_task", 4096, NULL, 2, NULL);
    // Start clock task
    xTaskCreate(&clock_task, "clock_task", 3072, NULL, 1, NULL);

    //=============================
    // End of Tasks initializations
    //=============================

}

//==========================
// Functions
//==========================

static void bufferUpdate(void){
	
	// obtain_time(&now, &timeInfo);
 	// strftime(strftime_db, sizeof(strftime_db), "%c", &timeInfo);
	time(&now); // Does not take into consideration the time zone

    sprintf(bufferData[bufferCounter],
    		"{ \"T\" : %d, \"H\" : %d, \"S\" : %d, \"D\" : %ld, \"DO\" : %ld, \"CO\" : %ld, \"GAS\" : %d }",
    		temperature, humidity, motorStatus, now, runningTime, continuousRunningTime, adc_reading);
    bufferCounter++;
}

static void get_last_value(void){


    // ======================================
    // Start GET request
    // ======================================

    // Get last value from firebase
    // obatin time (now, timeInfo)
    // Check if last value was in current day
    // If so update runningTime variable
    // Else, set it to zero

    // Currrently, we are not able to execute
    // the above algorithm, because the structure 
    // of the database.

    // ======================================
    // End of GET request
    // ======================================

}

static void update_daily(char *motorDailyAddress){

	#if CONFIG_debug
		ESP_LOGI(TAG_4, "Updating daily information");
	#endif

	// ======================================
    // Start POST request
    // ======================================

	time(&now); // Does not take into consideration the time zone

	char dailyData[40];

    sprintf(dailyData,"{ \"D\" : %ld, \"DO\" : %ld }", now, runningTime);
    // Create url
	sprintf(url, "https://%s/daily/%s.json",firebaseAddress, motorDailyAddress);

	// Struct which contains the HTTP configuration
    // https://docs.espressif.com/projects/esp-idf/en/latest/esp32/api-reference/protocols/esp_http_client.html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
    esp_http_client_config_t config = {
    .url = url,
    .event_handler = _http_event_handler,
    };

    // Call the client init passing the config struct to start a HTTP session
    // It returns a esp_http_client_handle_t that you must use as input to other functions in the interface
    // https://docs.espressif.com/projects/esp-idf/en/latest/esp32/api-reference/protocols/esp_http_client.html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
    esp_http_client_handle_t client = esp_http_client_init(&config);

    esp_http_client_set_method(client, HTTP_METHOD_POST);
    // client_open will open the connection, write all header strings and return ESP_OK if all went well
    // https://docs.espressif.com/projects/esp-idf/en/latest/esp32/api-reference/protocols/esp_http_client.html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
    if (esp_http_client_open(client, strlen(dailyData)) == ESP_OK) {
    	#if CONFIG_debug
    		ESP_LOGI(TAG_1, "Connection opened");
    	#endif
        esp_http_client_write(client, dailyData, strlen(dailyData));
        // https://docs.espressif.com/projects/esp-idf/en/latest/esp32/api-reference/protocols/esp_http_client.html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
        esp_http_client_fetch_headers(client);
        //ESP_LOGI(TAG_1, "HTTP POST Status = %d, content_length = %d", esp_http_client_get_status_code(client), esp_http_client_get_content_length(client));
        if (esp_http_client_get_status_code(client)==200){
        	#if CONFIG_debug
            	ESP_LOGI(TAG_1, "Message successfuly sent!");
            #endif
        }
        else {
        	#if CONFIG_debug
        	   	ESP_LOGI(TAG_1, "Sending message failed!");
        	#endif
        }
        //============
        // CONFIG_debug, but, in the future, perform a verification that the message was sent
        // char valor[77];
        // Read the stream of data
        // esp_http_client_read(client, valor, 77);
        // printf("%s\n",valor);
        // CONFIG_debug
        //============

        esp_http_client_close(client);
        esp_http_client_cleanup(client);
    
        runningTime=0;
        continuousRunningTime=0;
    }
    else {
    	#if CONFIG_debug
    	    ESP_LOGE(TAG_1, "Connection failed");
    	#endif
    }
    // ======================================
    // End of POST request
    // ======================================

}
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

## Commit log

2020-04-12 Updating temperature overnight, Good Night!
2020-04-23 Added variable to control which motor data show
2020-05-04 Added sp time, reset button, motor config menu
2020-05-04 Added sp time, reset button, get sp_time online
2020-05-05 Added sp time implementation and get front end motor status
2020-05-05 Added sp input form and a reset button
2020-05-05 Return to wifi connection every time due to problems
    [main.c]
2020-05-05 Added loading while reseting motor, front end control of status
2020-05-06 Added hardware version 0.1
    [BOM.csv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]
2020-05-06 Add links in BOM table
2020-05-08 Solved WiFi problem due to memory leaking
    [main.c]
2020-05-10 Update the daily operation of the motor
2020-05-11 Fixed bug of the first reading being null
    [main.c]
2021-03-15 Add version 2 of the board
    [BOM.csv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]
2021-03-15 Add interactive BOM
